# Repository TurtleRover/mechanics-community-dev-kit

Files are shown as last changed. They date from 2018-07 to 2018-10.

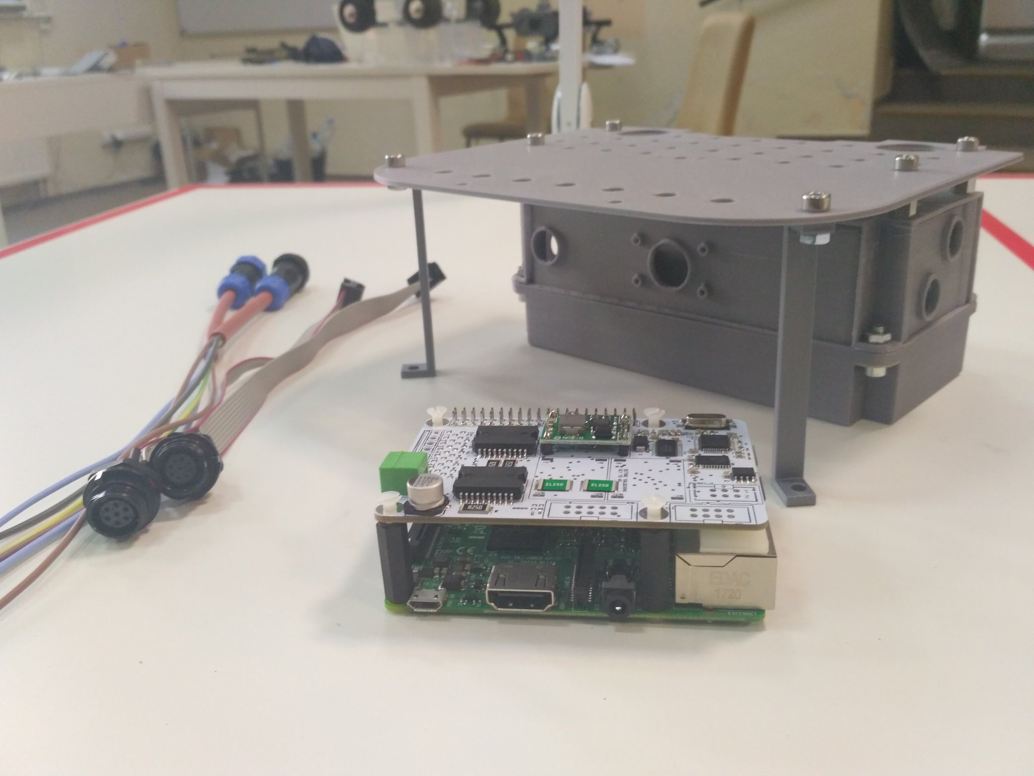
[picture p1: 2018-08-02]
comm-dev-kit-photo (1).jpg

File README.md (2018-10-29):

<p align="center">
  <a href="http://turtlerover.com" alt="Turtle Rover">Turtle Rover</a>
</p>
<h1 align="center">Mechanics: Community DevKit</h1>
<h4 align="center">A basic development kit. Includes 3D files and ready-to-print files</h4>

<p align="center">
  <a href="https://github.com/TurtleRover/mechanics-community-dev-kit/releases">
    </a>
  <a href="https://github.com/TurtleRover/mechanics-community-dev-kit/blob/master/LICENSE">
      
  </a>
  <a href="https://twitter.com/TurtleRover">
    
  </a>
</p>
<p align="center">
  <a href="http://turtlerover.com" alt="Website">Website</a> |
  <a href="https://www.facebook.com/TurtleRover/" alt="Facebook">Facebook</a> |
  <a href="https://www.youtube.com/channel/UCxukvEct3wP0S5FACa3uelA" alt="YouTube">YouTube</a>
</p>

# List of parts

## 3D-printed:
* 1x 03001 - Electronics box base
* 1x 03002 - Electronics box cover
* 1x 03003 - Mounting plate
* 2x 03005 - Support foot (2 pcs.)
* 2x 03006 - Electronics support (2 pcs.)

## Components:
* 1x [Shield](https://github.com/TurtleRover/electronics-shield)

## Fasteners:
* 6x M4x12 imbus screw
* 4x M4x12 threaded distance
* 8x M4x8 imbus screw
* 6x M4 hex-nut (or M4 square nut)
* 8x M2,5x8 philips-head screw
* 4x M2,5x20 threaded distance
* (optional) 2x Cable bushing SKINTOP ST-M LappKabel 53111000 (bushing + o-ring + nut)
* (optional) 5x Rubber bushing M12

## Cables and connectors:

* 1x Female connector WEIPU SP1310-S7II with tape
* 1x Female connector WEIPU SP1310-S9II with tape
* 1x Interface cable with WEIPU SP1310-P7II
* 1x Interface cable with WEIPU SP1310-P9II
* 1x 2-pin green connector
* 1x 8-pin green connector

## Not included and needed:
* 1x RaspberryPi 3B+
* 1x microSD card (8 GB)
* 1x Power adapter (12-24 DC; at least 1A)

## Tools needed:
* 1x microSD-to-SD card adapter
* 1x Philips-head screwdriver
* 1x Imbus screwdriver no. 3
* 1x Flat wrench no. 7
* 1x Double-sided tape
* 1x WD-40 can (or other lubricant)
* 1x Computer with a SD card slot

# Getting started

## Software upload:
1. [Download](https://drive.google.com/open?id=16_0G9UX7-NvIJFdP9mQDNYPm05ayJ65J) a newest TurtleOS SD card image. You can also [build it by yourself](https://github.com/TurtleRover/turtleos)
2. [Download Etcher](https://etcher.io/) (software to burn images to SD cards)
3. Using a microSD-to-SD card adapter, plug the card to your computer
4. Turn on Etcher and select the image. Select your drive and click 'Flash!'
5. It should take ca. 15 min to upload the image to the card
6. After a successful upload, unplug the microSD card and put it to your RaspberryPi

## Casing assembly:
1. Using 4x M4x8 imbus screws attach 4x M4x12 distances to a 03001 casing base (4 holes seen from the bottom)
2. Take 1x 7-pin WEIPU female connector and 1x 9-pin WEIPU female connector and, gently twisting their tapes, unscrew and separate nuts from them.
3. Push the connectors in slated holes on the bottom of 03001 base. Put the base in front of you with bottom up and SKINTOP bushings facing you. Left slated hole fits 9-pin WEIPU female connector and right hole 7-pin WEIPU female connector. Put nuts on the cables and screw them with your hand.
4. Using 4x M4x8 imbus screws assemble the casing (through distances) to 03003 mounting plate.
5. Using 1x M4x12 imbus screw and 1x M4 hex-nut (or square nut) assemble each of 03005 support foot to 03003 mounting plate front holes the ones facting rounded corners - left and right one).
6. Attach 2x 03005 electronics support to Turtle Shield using 4x M2,5x8 philips-head screws and 4x M2,5x20 threaded distances. The support should face the side of Turtle logo printed on the Shield.
7. Put Turtle Shield on top of RaspberryPi pins and push it gently to connect.
8. Screw remaining 4x M2,5x8 philips-head screws into RaspberryPi mounting holes.
9. Plug Turtle Shield USB connector to any socket in RaspberryPi.
10. Plug 8-pin green connector to Turtle Shield (you'll use it in the future to connect up to 4x DC motors)
11. Connect external power adapter cables to 2-pin green male connector (follow the mating connector description on the board).
12. Thread the power cable through on of two holes in the rear ofthe 03001 base.
13. Connect the 2-pin male connector to 2-pin female connetor on Turtle Shield.
14. Connect 7-pin and 9-pin WEIPU tape connectors to mating sockets in Turtle Shield.
15. Using double-sided tape - attach the legs of 3005 electronics support to the casing. Leave some place for USB connectors that could be connected to RaspberryPi.
16. Close the case with a 03002 cover using 4x M4x12 imbus screws and 4x M4 hex-head nuts (or square nuts).

## Optional items
There are (optional) items in the kit to provide some kind of watertightness to the casing. As it's tougher to attach external cables with the bushings in place, use them only after you get accustomed with the kit.
(optional) assembly:
1. Screw 2x SKINTOP Cable bushings using dedicated nuts and o-rings to rear panel of the casing base.
2. Push 5x Rubber bushing M12 using lubricant (WD-40 or other) into 4x side holes and 1x hole in the front (the one on the side of front panel)

## Accessing Turtle Control Software:
1. Plug the power adapter (turn on the Kit) and wait ca. 2-3 minutes for TurtleOS to set its WiFi.
2. On your computer, find a WiFi named: `TurtleRover-XXYY` (password: `password`).
3. Type: http://turtle.rover or http://10.0.0.1 in a browser (remember about 'http://').

Have fun!

## Additional description:
- Supports 1x USB camera, 4x DC motors and 3x servos in the pre-built interface
- RaspberryPi internal WiFi enabled
- WiFi name: `TurtleRover` ; password: `password`
- Type: http://turtle.rover or http://10.0.0.1 in a browser

Everything is licensed under MIT Open-source License. Feel free to use it, but remember to give credits on what you do.

Any help needed? Write: contact@turtlerover.com

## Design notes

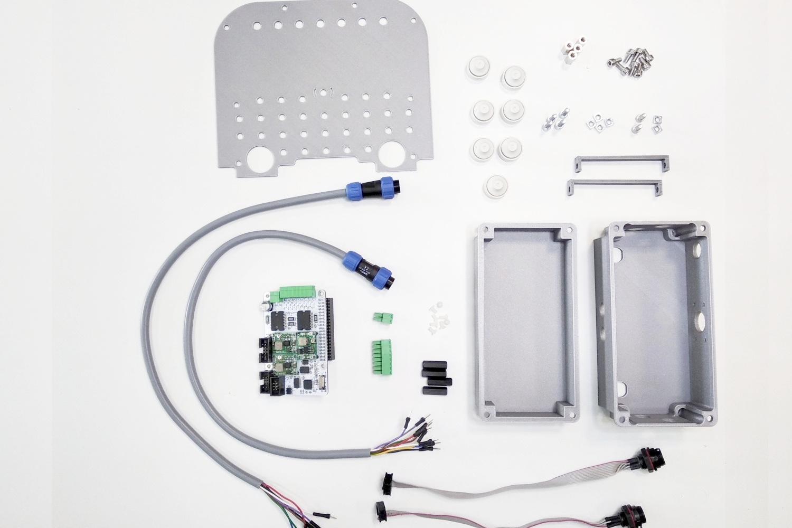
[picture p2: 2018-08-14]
comm-dev-kit-photo (2).jpg

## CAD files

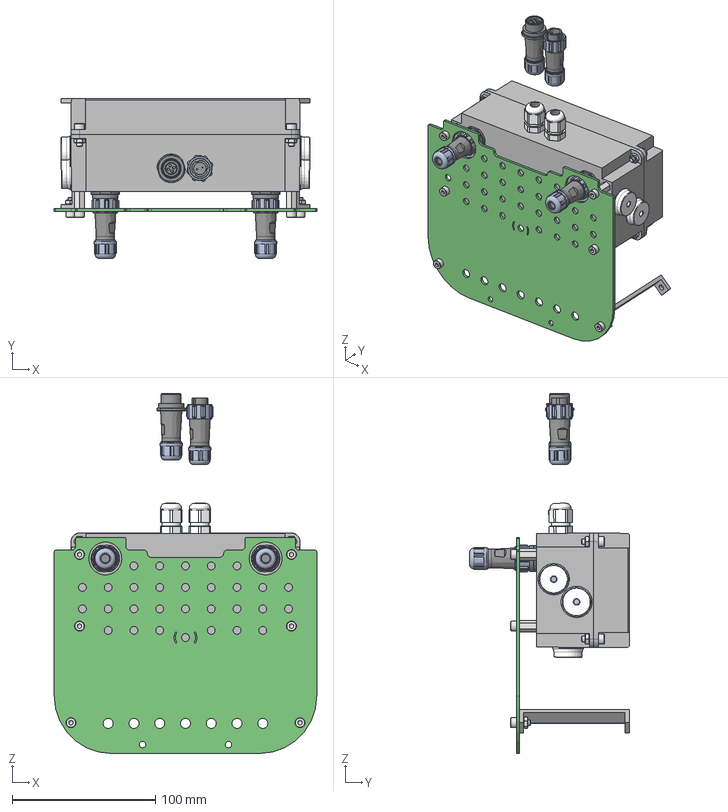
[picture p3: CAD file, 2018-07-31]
assembly/step/A3000.stp
183.4 x 111.8 x 251.5 mm
DIN 912 - M4 x 20 x 4
Turtle Hat
[E] RaspberryPi B+
gniazdo WEIPU SP1310-S7II
gniazdo WEIPU SP2111-S9II
wtyczka WEIPU SP1310-P7II
wtyczka WEIPU SP1310-P9II
Dławnica SKINTOP ST-M LappKabel 53111000 x 2
wtyczka WEIPU SP2110-P2II
gniazdo WEIPU SP2110-P4II
Rubber bushing M12 x 5
DIN 912 - M4 x 12 x 4
ISO 4032 - M4 x 10
ISO 7049 - ST 3,5 x 9,5 - F - Z x 3
DIN 912 - M4 x 10 x 2

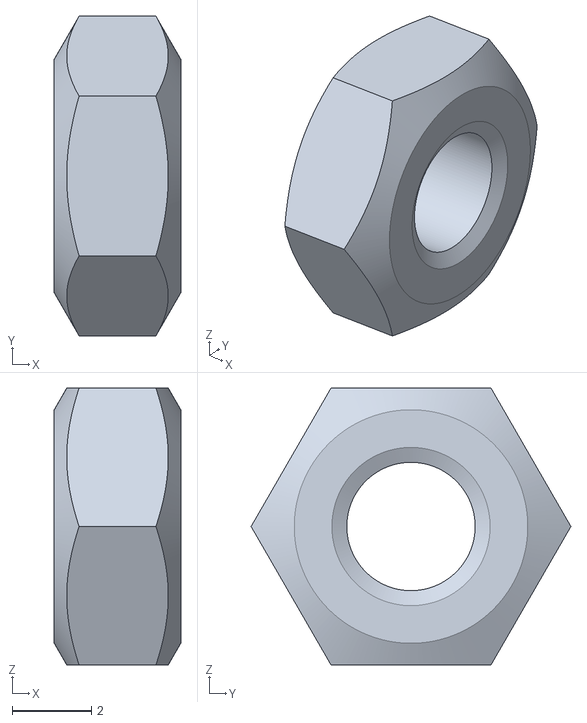
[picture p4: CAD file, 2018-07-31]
components-models/stl/DIN EN ISO 4032 - M4.stl
3.20 x 8.08 x 7.00

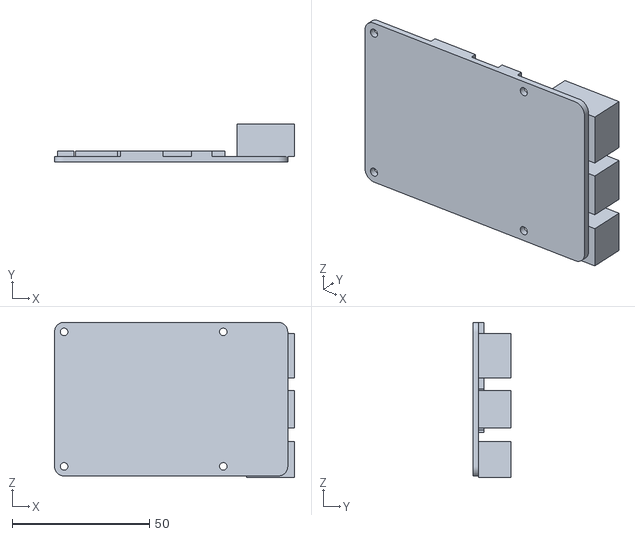
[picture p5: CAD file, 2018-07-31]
components-models/stl/[E] RaspberryPi B+.stl
87.5 x 14.0 x 56.6

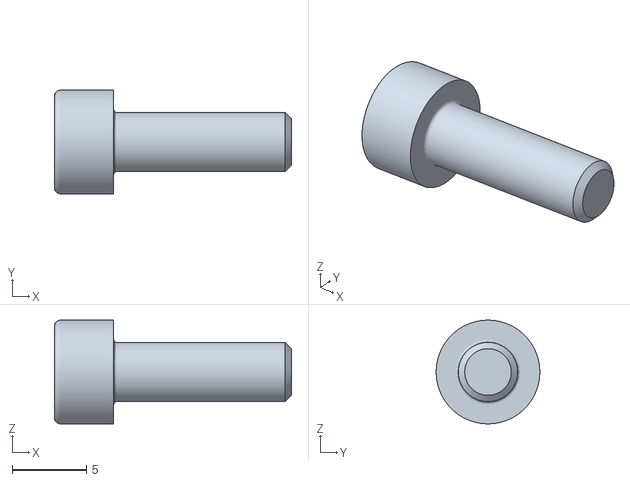
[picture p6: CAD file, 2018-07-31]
components-models/stl/DIN 912 - M4 x 0,7 x 12 x 10,25.stl
16.0 x 7.00 x 7.00

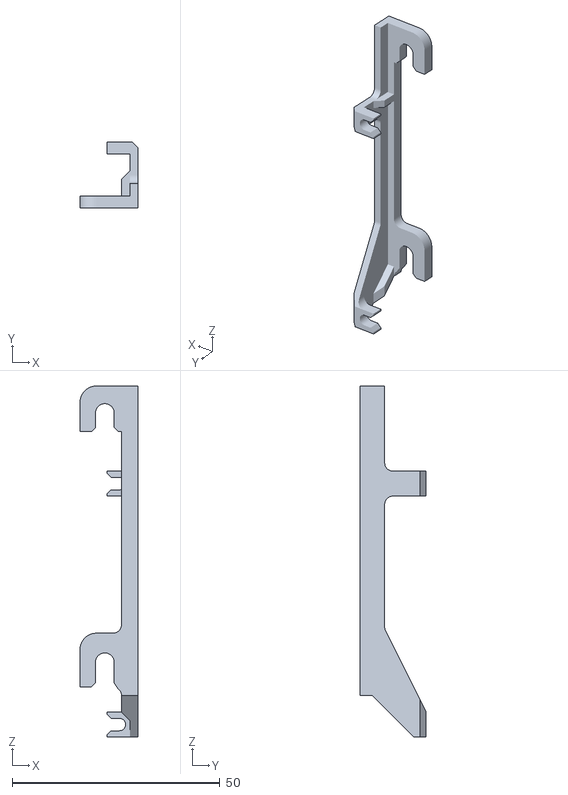
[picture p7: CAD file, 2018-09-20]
printed-files/stl/03008.stl
14.0 x 16.0 x 84.5

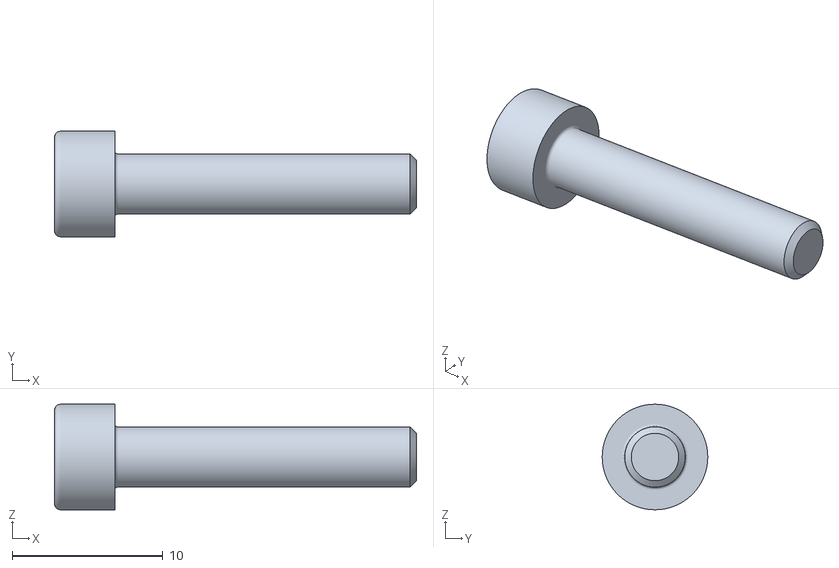
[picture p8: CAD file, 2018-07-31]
components-models/stl/DIN 912 - M4 x 0,7 x 20 x 18,25.stl
24.0 x 7.00 x 7.00

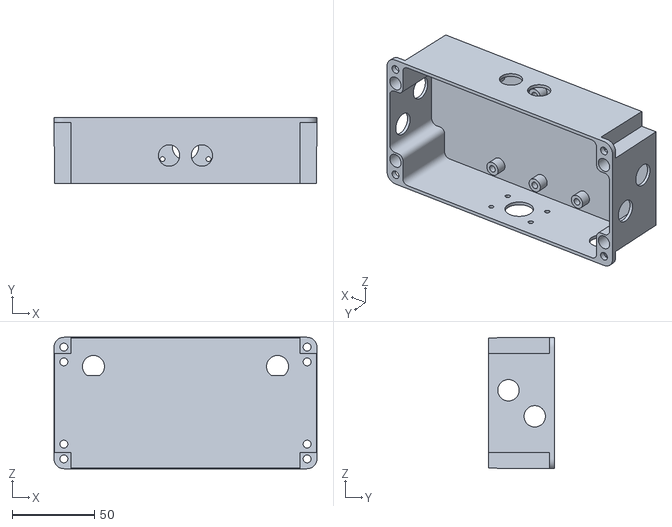
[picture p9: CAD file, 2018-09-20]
printed-files/stl/03001.stl
160.0 x 40.0 x 80.0

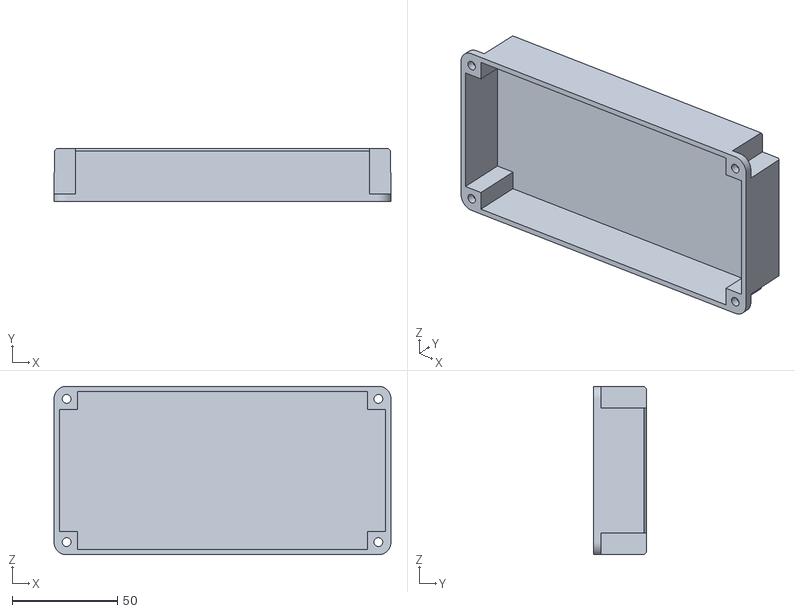
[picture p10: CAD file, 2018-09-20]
printed-files/stl/03002.stl
160.0 x 25.0 x 80.0

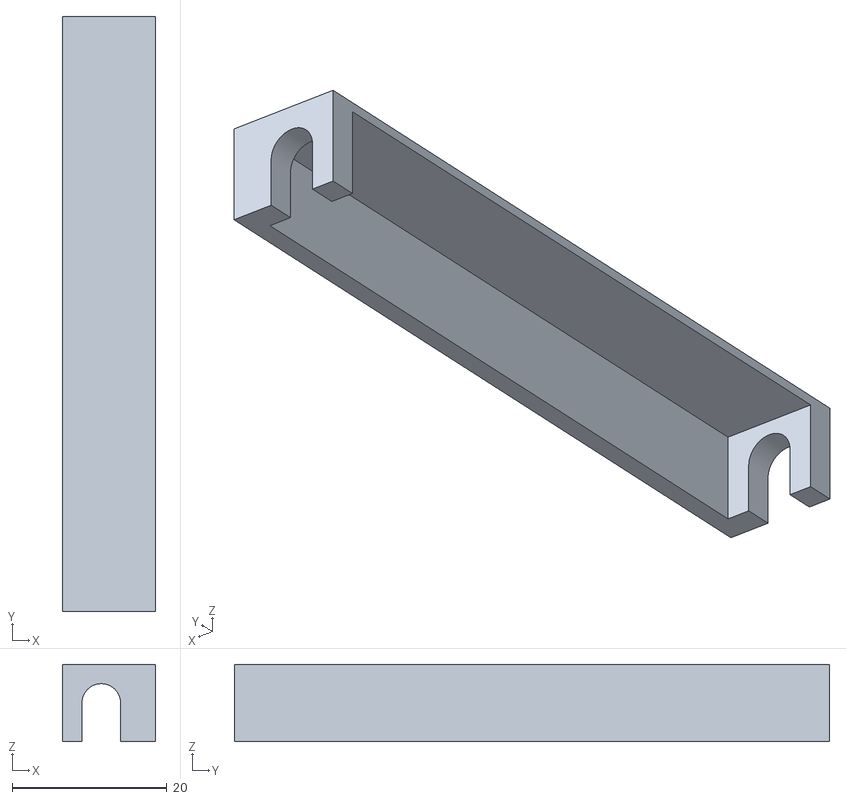
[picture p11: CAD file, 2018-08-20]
printed-files/stl/03005.stl
12.0 x 77.0 x 10.0

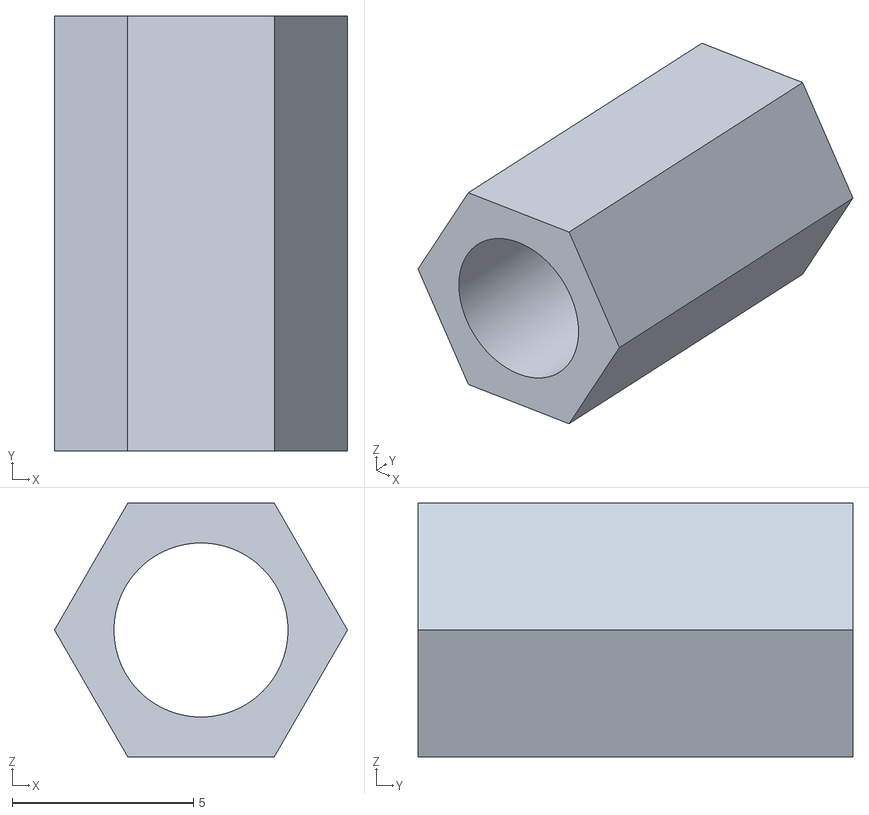
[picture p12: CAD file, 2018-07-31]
printed-files/stl/03004.stl
8.08 x 12.0 x 7.00

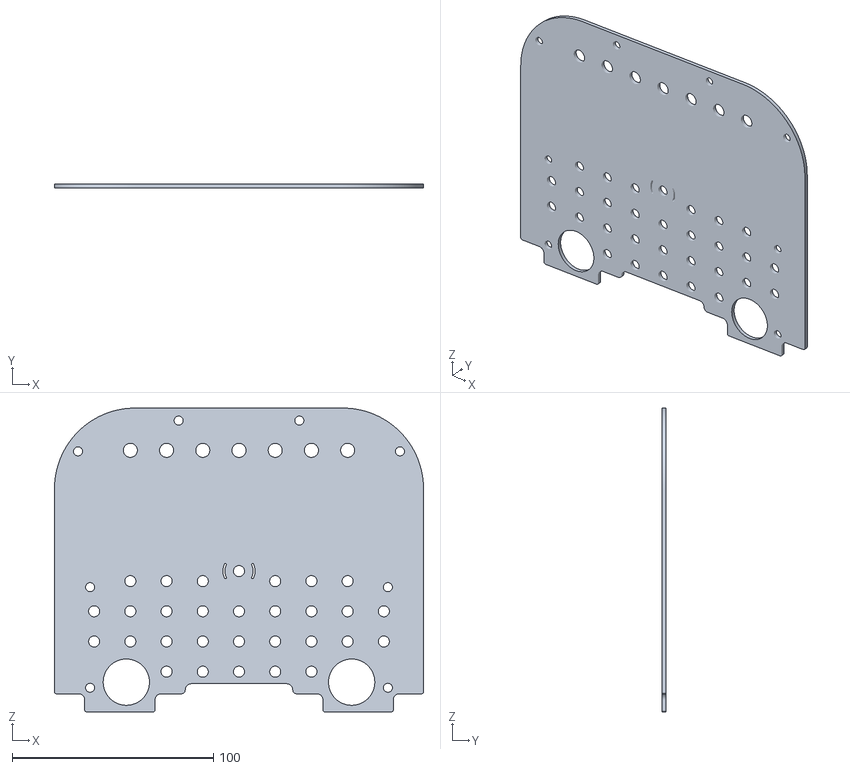
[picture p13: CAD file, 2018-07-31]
printed-files/stl/03003.stl
183.4 x 2.00 x 151.0

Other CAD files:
printed-files/stl/03007.stl

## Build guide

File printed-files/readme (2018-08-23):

Index table and print time (Prusa MK3; 0.2; support on; 100% infill):

3001 - Electronics box base - 9h 43m
3002 - Electronics box cover -  6h 55m
3003 - Mounting plate - 3h 00m
3004 - Distance - 0h 09m (4 pcs. needed; 4x = 0h 34m)
3005 - Support foot - 0h 24m (2pcs. needed; 2x = 0h 49m)
3007 - Electronics support A - 0h 25m
3008 - Electronics support B - 0h 25m

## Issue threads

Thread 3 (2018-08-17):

Camera holes are too tight

SzymonDzw, 2018-08-17:
They need to be redrilled with fi3 drill - need to change 3d-model.

Closed 2018-08-20.

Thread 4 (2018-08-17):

Connector holes too tight

SzymonDzw, 2018-08-17:
Force needed to push connectors to the casing. Doable, but...

Closed 2018-08-20.

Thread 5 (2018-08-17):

Cover to base screw holes jamming

SzymonDzw, 2018-08-17:
Holes too tight - problems with 3d-print.

Closed 2018-08-20.

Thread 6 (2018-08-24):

Weak spots in electronics support

SzymonDzw, 2018-08-24:
mechanics-community-dev-kit/printed-files/stl/03007.stl

The hooks for attaching the item to electronics casing break easily.

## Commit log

2018-08-06 Strengthen the prints
    Added ribs to make 03005 legs and 03003 platform stiffer.
    [03005.stl]
2018-08-06 Upload - electronics support
    [03006.stl]
2018-08-06 Mounting holes fixed
    A bridge near mounting holes extends now to the cover. Now the casing can be sealed if sealant added to a meeting surface (base - cover).
    [03001.stl]
2018-08-20 Holes issues solved
    [03001.stl]
2018-08-20 Bug fixed
    [03001.stl]
2018-08-23 03007 and 03008 added
    [03006.stl, 03007.stl, 03008.stl]
2018-09-20 Changed thickness and mounting points
    03001 and 03002 changed wall thickness to cut printing time.
    03007 03008 - changed mounting direction to fit cabling issuess
    [03001.stl, 03002.stl, 03007.stl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]
2018-10-22 Better formatting, Hat → Shield
